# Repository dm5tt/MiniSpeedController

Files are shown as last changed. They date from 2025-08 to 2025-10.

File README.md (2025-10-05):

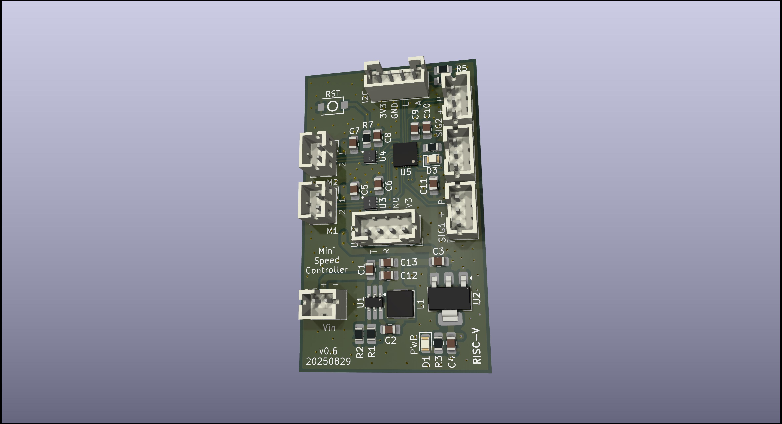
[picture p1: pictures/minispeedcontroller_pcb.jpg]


# Mini (RISC-V DC-Motor) Speed Controller

This project implements a compact DC motor speed controller using a RISC-V microcontroller. 

It is designed for speed control via pulse feedback from a light barrier and communicates through a serial interface. Additional  sensors can be attached using I2C.

Beware that the entire PCB isn't a masterpiece as this is just for technology evaluation. 

## Why this thing?

Mostly for playing around with very cheap RISC-V microcontrollers and an execise for C/Rust with very limited resources. It can be used for controlling simple toy robot chassis that usually have two DC motors with light barriers which can be used as feedback loop for a speed control algorithm.

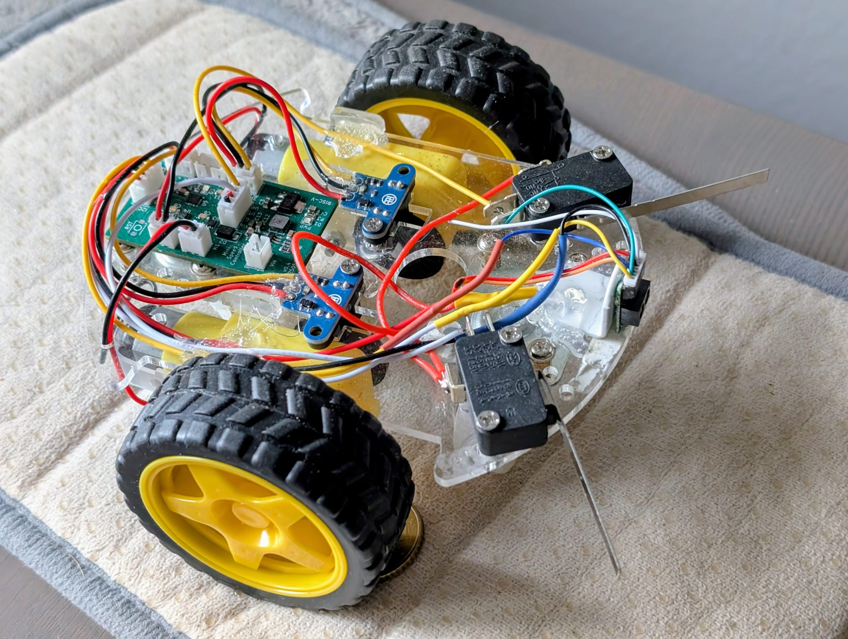
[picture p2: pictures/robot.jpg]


## System Overview

#### Power Supply
  - AP62300 (3A Buck Converter) → 7V rail (for DC motors)  
  - AMS1117-3.3 (LDO Regulator) → 3.3V rail (for microcontroller and motor driver logic)  

#### WCH CH32V003 Microcontroller 
  - 48 MHz RISC-V core  
  - 16 KB Flash / 2 KB SRAM  
  - Powered from 3.3V rail
    
#### Texas Instruments DRV8837GSGR 
  - Brushed DC motor driver  
  - 1.8A continuous current capability  
  - Logic powered from 3.3V rail
  - DC motors powered from 7V rail

### Pin Configuration

#### Motor Controller 1
| Pin | Meaning |
|-----|---|
| PC5 | motcon1_sleep |
| PC6 | motcon1_in2 |
| PD2 | motcon1_pwm_in1  |

#### Motor Controller 2
| Pin | Meaning |
|-----|---|
| PC3 | motcon2_sleep |
| PC4 | motcon2_in2 |
| PA1 | motcon2_pwm_in1  |

#### PWM Speed Inputs
| Pin | Meaning |
|-----|---|
| PC0 | pwm_speed_input1 |
| PD3 | pwm_speed_input2 |

#### Communication Interfaces
| Pin | Meaning |
|-----|---|
| PC1 | i2c_sda |
| PC2 | i2c_scl |
| PD5 | usart_tx |
| PD6 | usart_rx |

#### Debug & Reset
| Pin | Meaning |
|-----|---|
| PD1 | SWDIO |
| PD7 | nRST |

#### Indicators
| Pin | Meaning |
|-----|---|
| PA2 | status_led |

### Unused / Spare
| Pin | Meaning |
|-----|---|
| PC7 | X |
| PD0 | X |
| PD4 | X |

# Verification

[Hardware Verification v0.4](EVALUATION-v0.4.md)

# License

CERN OHL v2 – Strongly Reciprocal (S)

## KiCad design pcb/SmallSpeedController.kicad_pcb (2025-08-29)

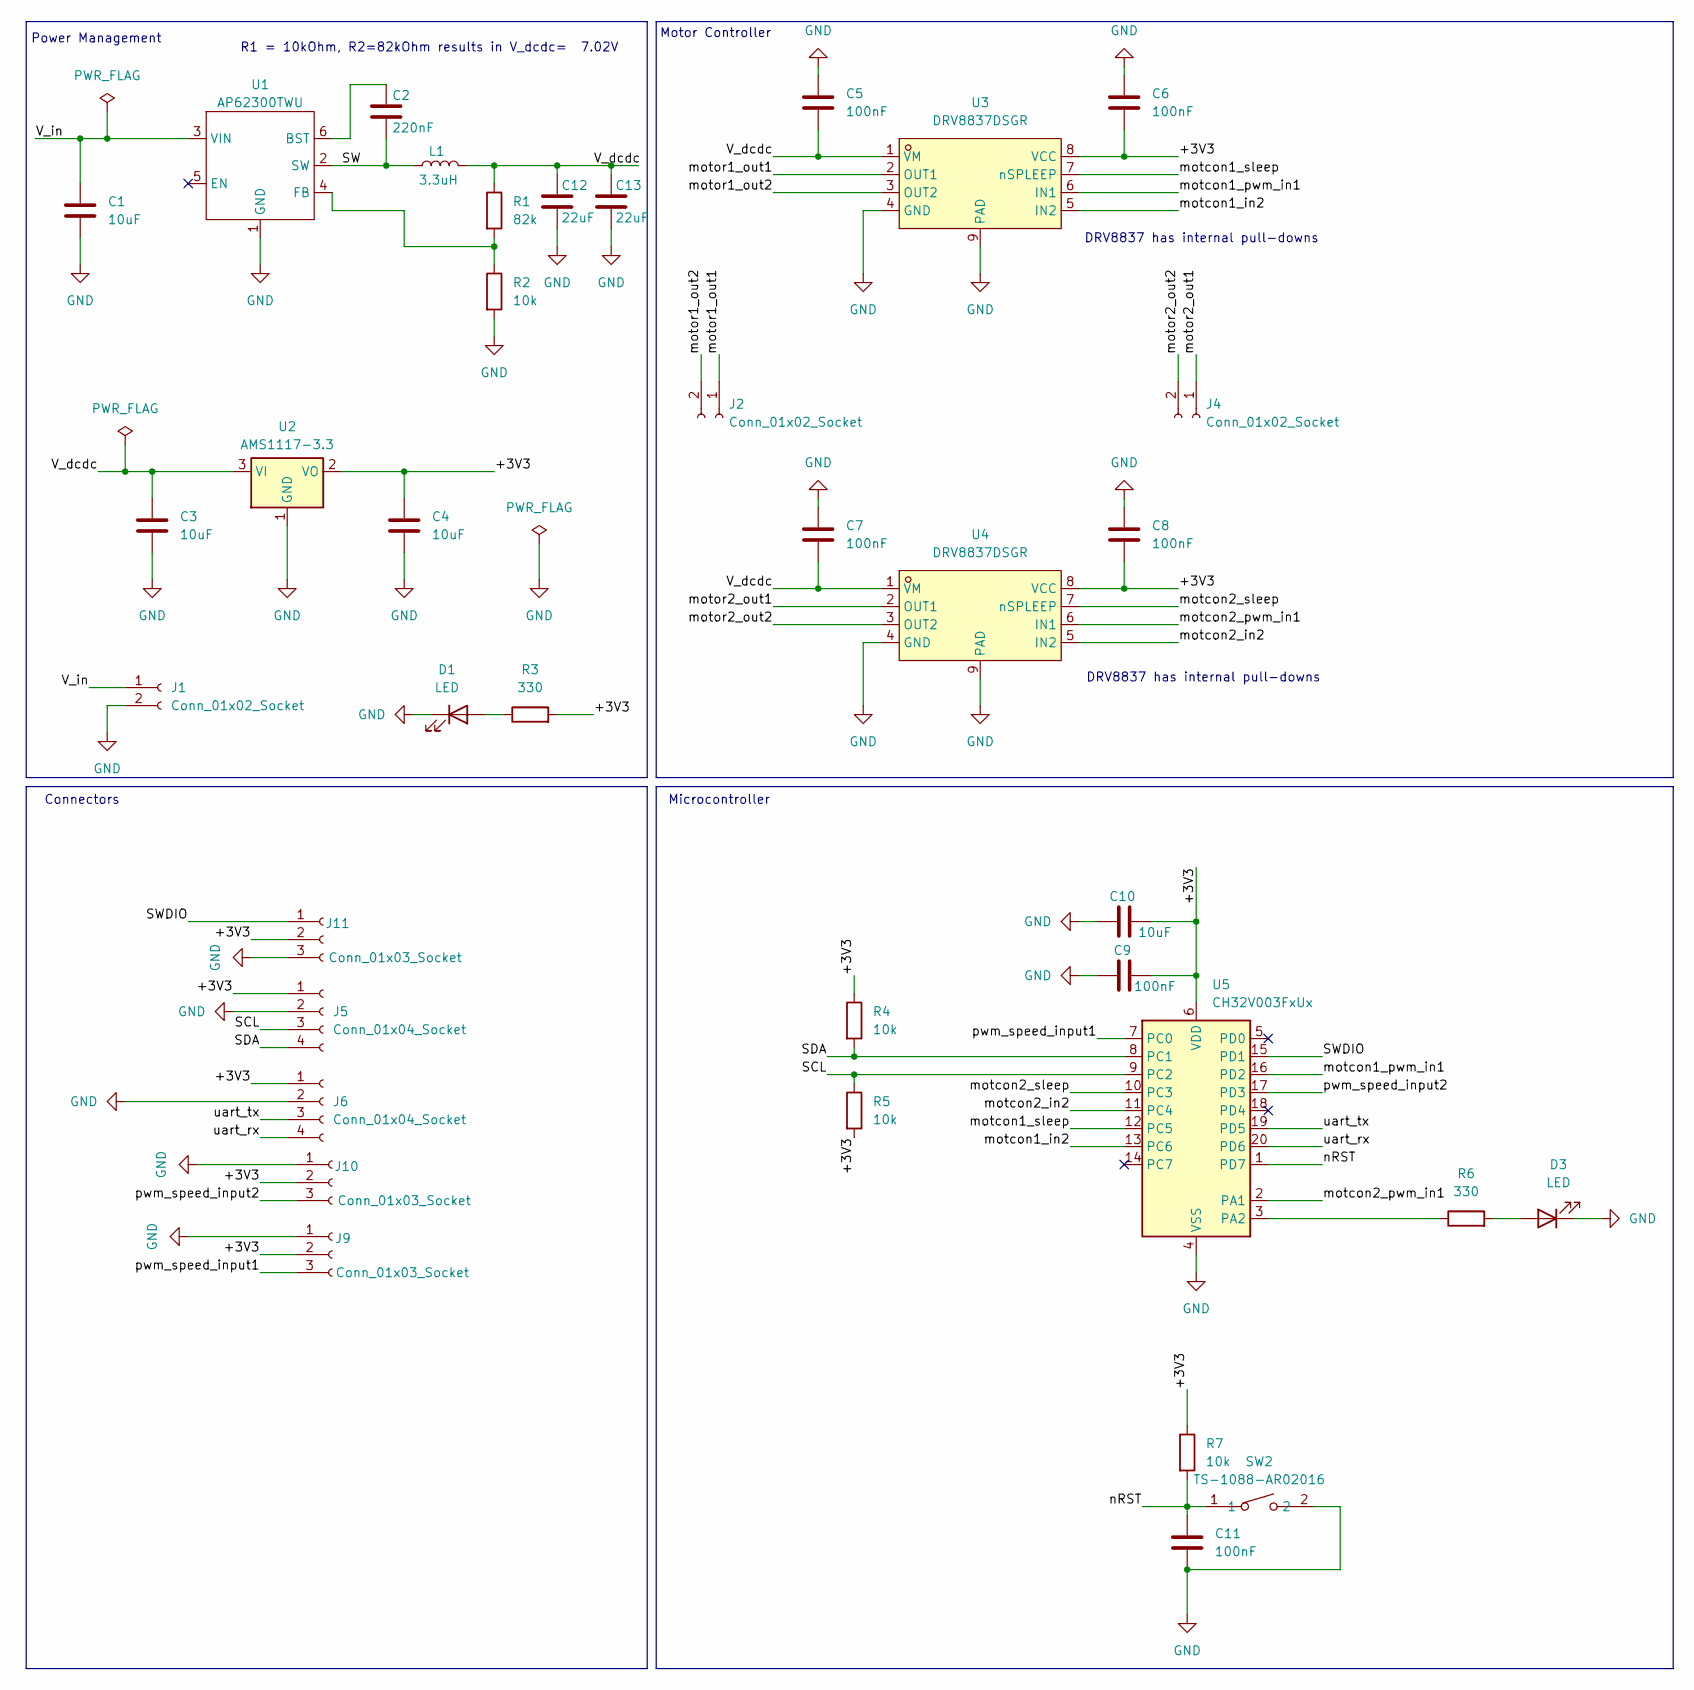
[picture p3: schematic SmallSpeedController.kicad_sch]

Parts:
C1, C3, C4, C10: 10uF; C_0805_2012Metric_Pad1.18x1.45mm_HandSolder
C2: 220nF; C_0805_2012Metric_Pad1.18x1.45mm_HandSolder
C5, C6, C7, C8, C9, C11: 100nF; C_0805_2012Metric_Pad1.18x1.45mm_HandSolder
C12, C13: 22uF; C_0805_2012Metric_Pad1.18x1.45mm_HandSolder
D1, D3: LED; LED_0805_2012Metric
J1, J2, J4: Conn_01x02_Socket; JST_PH_B2B-PH-K_1x02_P2.00mm_Vertical
J5, J6: Conn_01x04_Socket; JST_PH_B4B-PH-K_1x04_P2.00mm_Vertical
J9, J10, J11: Conn_01x03_Socket; JST_PH_B3B-PH-K_1x03_P2.00mm_Vertical
L1: 3.3uH; CPX0420
R1: 82k; R_0805_2012Metric_Pad1.20x1.40mm_HandSolder
R2, R4, R5, R7: 10k; R_0805_2012Metric_Pad1.20x1.40mm_HandSolder
R3, R6: 330; R_0805_2012Metric_Pad1.20x1.40mm_HandSolder
SW2: TS-1088-AR02016; SW-SMD_L3.9-W3.0-P4.45; LCSC Part C720477
U1: AP62300TWU; TSOT-23-6_HandSoldering
U2: AMS1117-3.3; SOT-223-3_TabPin2
U3, U4: DRV8837DSGR; WSON-8_L2.0-W2.0-P0.50-TL-EP; LCSC Part C39159
U5: CH32V003FxUx; QFN-20-1EP_3x3mm_P0.4mm_EP1.65x1.65mm

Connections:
/+3V3: C4.1, C6.2, C8.2, C9.2, C10.2, J5.1, J6.1, J9.2, J10.2, J11.2, R3.2, R4.1, R5.2, R7.1, U2.2 (VO), U3.8 (VCC), U4.8 (VCC), U5.6 (VDD)
/SCL: J5.3, R5.1, U5.9 (PC2)
/SDA: J5.4, R4.2, U5.8 (PC1)
/SW: C2.2, L1.1, U1.2 (SW)
/SWDIO: J11.1, U5.15 (PD1)
/V_dcdc: C3.1, C5.2, C7.2, C12.1, C13.1, L1.2, R1.1, U2.3 (VI), U3.1 (VM), U4.1 (VM)
/V_in: C1.1, J1.1, U1.3 (VIN)
/motcon1_in2: U3.5 (IN2), U5.13 (PC6)
/motcon1_pwm_in1: U3.6 (IN1), U5.16 (PD2)
/motcon1_sleep: U3.7 (nSPLEEP), U5.12 (PC5)
/motcon2_in2: U4.5 (IN2), U5.11 (PC4)
/motcon2_pwm_in1: U4.6 (IN1), U5.2 (PA1)
/motcon2_sleep: U4.7 (nSPLEEP), U5.10 (PC3)
/motor1_out1: J2.1, U3.2 (OUT1)
/motor1_out2: J2.2, U3.3 (OUT2)
/motor2_out1: J4.1, U4.2 (OUT1)
/motor2_out2: J4.2, U4.3 (OUT2)
/nRST: C11.1, R7.2, SW2.1, U5.1 (PD7)
/pwm_speed_input1: J9.3, U5.7 (PC0)
/pwm_speed_input2: J10.3, U5.17 (PD3)
/uart_rx: J6.4, U5.20 (PD6)
/uart_tx: J6.3, U5.19 (PD5)
GND: C1.2, C3.2, C4.2, C5.1, C6.1, C7.1, C8.1, C9.1, C10.1, C11.2, C12.2, C13.2, D1.1 (K), D3.1 (K), J1.2, J5.2, J6.2, J9.1, J10.1, J11.3, R2.2, SW2.2, U1.1 (GND), U2.1 (GND), U3.4 (GND), U3.9 (PAD), U4.4 (GND), U4.9 (PAD), U5.4 (VSS), U5.21 (VSS)
unnamed: D1.2 (A), R3.1
unnamed: D3.2 (A), R6.2
unnamed: C2.1, U1.6 (BST)
unnamed: R1.2, R2.1, U1.4 (FB)
unnamed: R6.1, U5.3 (PA2)

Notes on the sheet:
Microcontroller
Motor Controller
DRV8837 has internal pull-downs
R1 = 10kOhm, R2=82kOhm results in V_dcdc= 7.02V
Power Management
Connectors

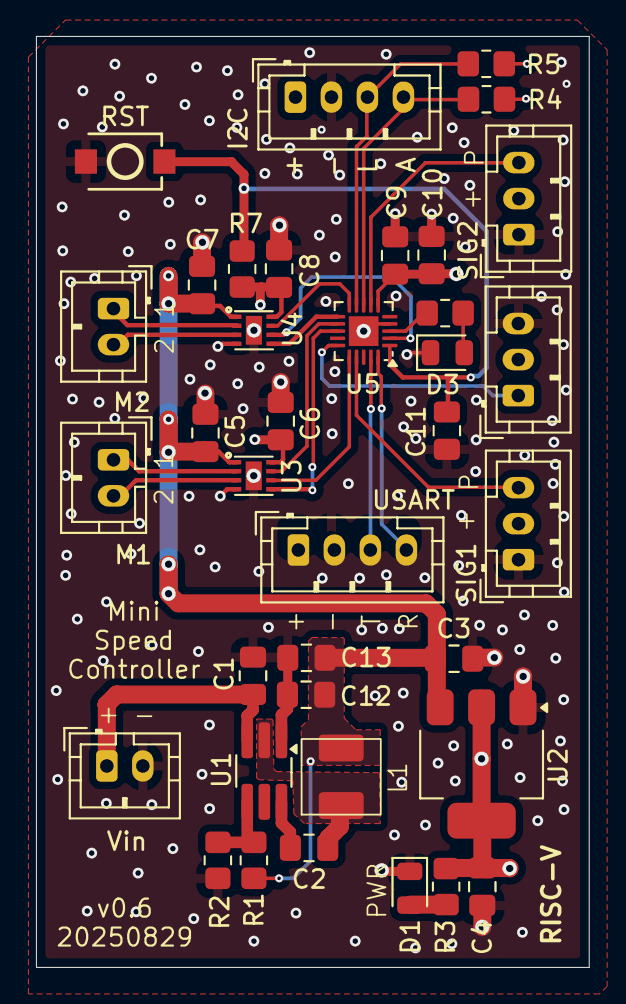
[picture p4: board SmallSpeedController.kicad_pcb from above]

Board: 4 copper layers, 30.7 x 51.7 mm, 37 parts (0 on the bottom side), 28 nets.

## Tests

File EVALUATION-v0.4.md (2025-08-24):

# Hardware verification v0.4

List:
 - ✅ DCDC
 - ✅ LDO
 - ✅ CH32V003
 - ✅ DRV8837GSGR

## First Power-Up Test of the WCH CH32V003
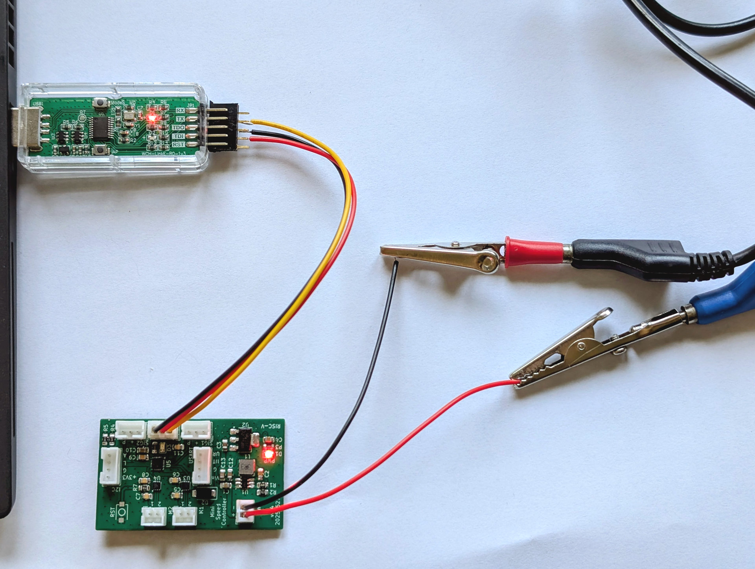
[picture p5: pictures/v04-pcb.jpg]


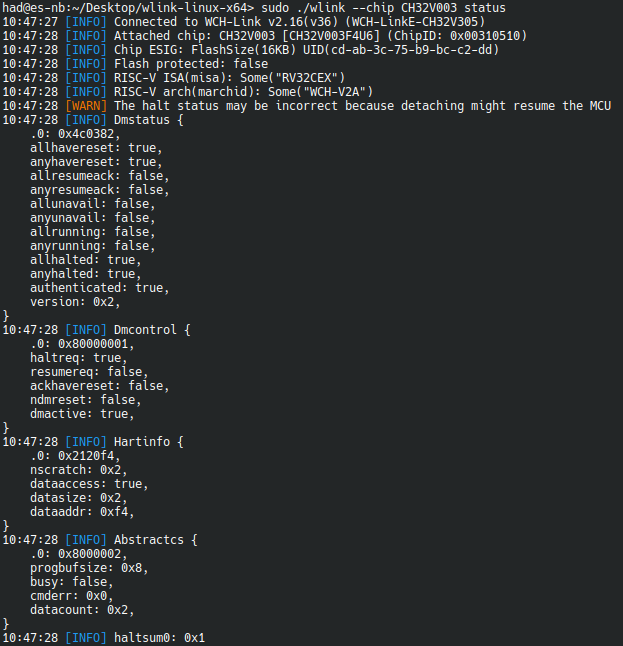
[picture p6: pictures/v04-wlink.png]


## Motor Spinning

See [this video](pictures/motor_spinning_no_meta.mp4).

Roughly 1.4A@12V was consumed in this rather extreme movement test.

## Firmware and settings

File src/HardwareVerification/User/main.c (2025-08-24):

#include "debug.h"

#include "minispeedcontroller_led.h"
#include "minispeedcontroller_usart.h"
#include "minispeedcontroller_motcon.h"

int main (void) {
    NVIC_PriorityGroupConfig (NVIC_PriorityGroup_1);
    SystemCoreClockUpdate();
    Delay_Init();

    minispeedcontroller_led_init();
    minispeedcontroller_motcon_init();
    minispeedcontroller_usart_init();

    printf ("SystemClk:%d\r\n", SystemCoreClock);
    printf ("ChipID:%08x\r\n", DBGMCU_GetCHIPID());

    while (1) {
        minispeedcontroller_led_set (true);
        minispeedcontroller_motcon_m1_step();
        minispeedcontroller_led_set (false);
    }
}

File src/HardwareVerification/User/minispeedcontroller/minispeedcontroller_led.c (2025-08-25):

#include "minispeedcontroller_led.h"

#include <ch32v00x.h>

#define MINISPEEDCONTROLLER_LED_PIN GPIO_Pin_2 /* PA2 */

void minispeedcontroller_led_init (void) {
    /* Disable OSC so we can use PA1 and PA2 as I/O */
    AFIO->PCFR1 &= ~(1U << 15);

    GPIO_InitTypeDef GPIO_InitStructure = {0};

    RCC_APB2PeriphClockCmd (RCC_APB2Periph_GPIOA, ENABLE);
    GPIO_InitStructure.GPIO_Pin = MINISPEEDCONTROLLER_LED_PIN;
    GPIO_InitStructure.GPIO_Mode = GPIO_Mode_Out_PP;
    GPIO_InitStructure.GPIO_Speed = GPIO_Speed_30MHz;
    GPIO_Init (GPIOA, &GPIO_InitStructure);
}

void minispeedcontroller_led_set (_Bool state) {
    GPIO_WriteBit (GPIOA, MINISPEEDCONTROLLER_LED_PIN, state ? Bit_SET : Bit_RESET);
}

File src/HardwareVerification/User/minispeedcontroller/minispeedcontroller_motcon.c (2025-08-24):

#include "minispeedcontroller_motcon.h"

#include <ch32v00x.h>

#include <stdbool.h>
#include <stdint.h>


#define MINISPEEDCONTROLLER_MOTCON2_PIN_SLEEP GPIO_Pin_3    // PC3
#define MINISPEEDCONTROLLER_MOTCON2_PIN_IN2 GPIO_Pin_4      // PC4
#define MINISPEEDCONTROLLER_MOTCON2_PIN_PWM_IN1 GPIO_Pin_1  // PA1

void minispeedcontroller_motcon_init() {
    GPIO_InitTypeDef GPIO_InitStructure = {0};

    RCC_APB2PeriphClockCmd (RCC_APB2Periph_GPIOC, ENABLE);
    GPIO_InitStructure.GPIO_Pin = MINISPEEDCONTROLLER_MOTCON2_PIN_SLEEP | MINISPEEDCONTROLLER_MOTCON2_PIN_IN2;
    GPIO_InitStructure.GPIO_Mode = GPIO_Mode_Out_PP;
    GPIO_InitStructure.GPIO_Speed = GPIO_Speed_30MHz;
    GPIO_Init (GPIOC, &GPIO_InitStructure);

    RCC_APB2PeriphClockCmd (RCC_APB2Periph_GPIOA, ENABLE);
    GPIO_InitStructure.GPIO_Pin = MINISPEEDCONTROLLER_MOTCON2_PIN_PWM_IN1;
    GPIO_InitStructure.GPIO_Mode = GPIO_Mode_Out_PP;
    GPIO_InitStructure.GPIO_Speed = GPIO_Speed_30MHz;
    GPIO_Init (GPIOA, &GPIO_InitStructure);

    GPIO_WriteBit (GPIOC, MINISPEEDCONTROLLER_MOTCON2_PIN_SLEEP, Bit_SET);

}

void minispeedcontroller_motcon_m1_step() {
    GPIO_WriteBit (GPIOC, MINISPEEDCONTROLLER_MOTCON2_PIN_IN2, Bit_RESET);

    GPIO_WriteBit (GPIOA, MINISPEEDCONTROLLER_MOTCON2_PIN_PWM_IN1, Bit_SET);
    Delay_Ms (50);
    GPIO_WriteBit (GPIOA, MINISPEEDCONTROLLER_MOTCON2_PIN_PWM_IN1, Bit_RESET);
    Delay_Ms (50);

    GPIO_WriteBit (GPIOC, MINISPEEDCONTROLLER_MOTCON2_PIN_IN2, Bit_SET);


    GPIO_WriteBit (GPIOA, MINISPEEDCONTROLLER_MOTCON2_PIN_PWM_IN1, Bit_SET);
    Delay_Ms (50);
    GPIO_WriteBit (GPIOA, MINISPEEDCONTROLLER_MOTCON2_PIN_PWM_IN1, Bit_RESET);
    Delay_Ms (50);

}

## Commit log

2025-08-25 minispeedcontroller, led: remove broken test code
    [minispeedcontroller_led.c]
2025-08-29 pcb: give 3v3 on the UART connector and get rid of diode
    [SmallSpeedController.kicad_pcb, SmallSpeedController.kicad_sch]
2025-08-29 pcb: harmonize silk prints, also use double vias for 7V rails
    [SmallSpeedController.kicad_pcb]
2025-08-29 pcb: non functional changes
    [SmallSpeedController.kicad_pcb]
2025-08-29 pictures: update pcb picture
2025-08-29 pcb: restore symmetry after diode was removed
    [SmallSpeedController.kicad_sch]
